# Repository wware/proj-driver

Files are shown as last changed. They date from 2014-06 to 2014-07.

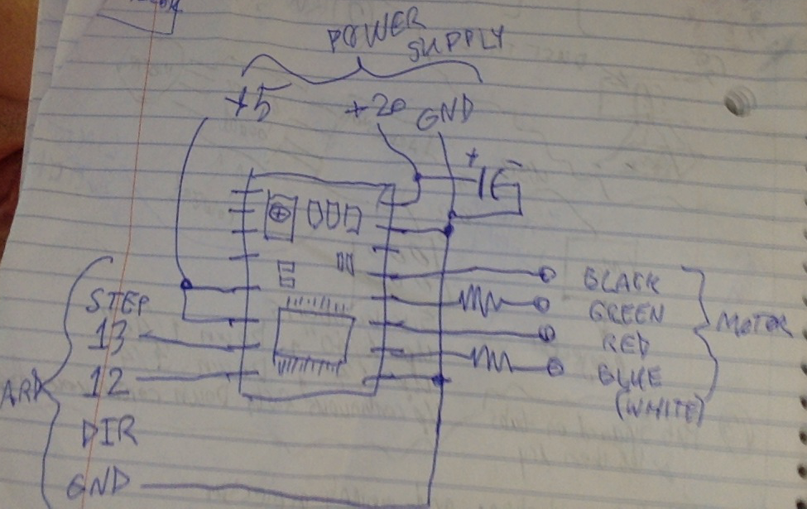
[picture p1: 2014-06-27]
arduino/StepperDriverSchematic.png

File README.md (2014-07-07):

Stereolithographic printer
==

[Blog post](http://willware.blogspot.com/2014/07/homebrew-stereolithographic-3d-printer.html)

A picture of the printer What it looks like

Initially I tried shooting the projector up through the bottom of a glass pie plate, and followed examples of coating the inside of the pie
plate with Sylgard 184. But I couldn't get the Sylgard to work correctly; the cured resin kept sticking to it instead of sticking to my
build platform. So I took a page from the [Peachy Printer](https://www.youtube.com/watch?v=80HsW4HmUes) and projected downwards into a
bucket where a layer of resin floats on a larger quantity of salt water, because resin is expensive and salt water is very cheap.

My long-term intent, once I get several bugs and issues sorted out, is to publish plans, schematics, and software on
[Github](https://github.com) and [Instructables](http://instructables.com) or similar websites, and put the entire thing either in the
public domain or under some reasonably permissive [Creative Commons](http://creativecommons.org/) license like
[BY-SA](http://creativecommons.org/licenses/by-sa/3.0/).

Projector
--

InFocus IN114A, unmodified, 3000 lumens, 1024x768 resolution, HDMI input, 190 watts, 110 vac, $349 with $6 shipping

* http://www.newegg.com/Product/Product.aspx?Item=0B1-00PJ-00003
* http://www.infocus.com/projectors/product?pn=IN114A

Browser stuff
--

You need a browser window on the Mac that can be updated when necessary, and you position that browser window image under the resin tub. This runs off a little CherryPy server on the Mac. The home page that the browser visits has Javascript which hits an endpoint asking for an numerical index and a number of seconds. This polling happens fairly frequently (once or twice a second).
The file with that metadata is at `static/image.info` and is expos1ed with a URL of `/info`. The image is stored at `static/image.png` and
is exposed with a URL of `/image`. You don't want to use CherryPy's static mechanism to read these files, because they get cached and then
you don't get updated when they change.

If the JS hasn't seen that index before (which simply increments) then it un-hides an image element for that number of seconds.

The background of the web page is black so as to not cure any resin unnecessarily.

I might need [templating](https://bitbucket.org/Lawouach/cherrypy-recipes/src/tip/web/templating/).

On the Mac, use Cmd-Shift-F to make a browser tab take up the full screen.

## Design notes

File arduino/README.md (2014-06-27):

Arduino code
==

The Arduino has the job of driving the stepper. It communicates over USB-serial with the
host machine. (The host machine also drives the projector.) I'm using a Macbook for the
host machine but there is no reason you couldn't use a Windows or Linux machine.

The serial protocol works like this. You type a letter (j, J, k, K, U, I) and in respponse
the motor moves the carriage up or down by some amount. The mnemonic is the vi commands:
Lower-case j and k respectively move the carriage down and up by 1/40 inch. Upper-case J
and K respectively move the carriage down and up by 1/4 inch. Upper-case U and I
respectively move the carriage down and up by 2.5 inches. Since the threaded rod is
20 threads per inch, the small step is a half-rotation of the threaded rod, or 90 steps
of the NEMA-23 stepper motor.

Any other characters typed will be echoed, but won't move the motor. These letters will
be echoed at the end of the carriage movement. While the carriage is in motion, any
characters typed should be ignored.

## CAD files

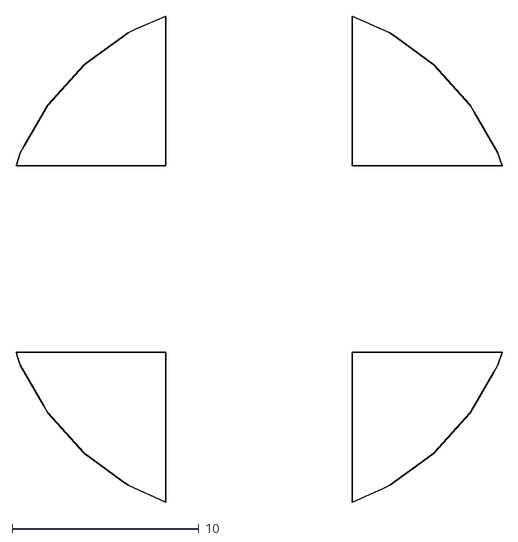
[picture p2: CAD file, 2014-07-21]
foo.dxf
26.0 x 26.0

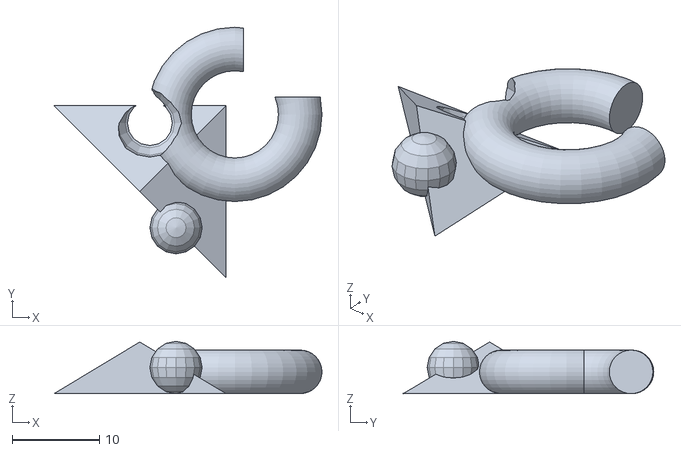
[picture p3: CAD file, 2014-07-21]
example.stl
30.7 x 28.7 x 6.00

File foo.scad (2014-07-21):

module example002()
{
    intersection() {
        difference() {
            union() {
                cube([30, 30, 30], center = true);
                translate([0, 0, -25])
                    cube([15, 15, 50], center = true);
            }
            union() {
                cube([50, 10, 10], center = true);
                cube([10, 50, 10], center = true);
                cube([10, 10, 50], center = true);
            }
        }
        translate([0, 0, 5])
            cylinder(h = 50, r1 = 20, r2 = 5, center = true);
    }
}

projection(cut = true) example002();

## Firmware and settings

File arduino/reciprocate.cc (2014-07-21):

int DIRECTION = 12, STEP = 13;

void setup() {
    pinMode(STEP, OUTPUT);
    pinMode(DIRECTION, OUTPUT);
    digitalWrite(STEP, LOW);
    digitalWrite(DIRECTION, LOW);
}

void briefWait() {
    delayMicroseconds(1000);
}

void run_motor(int dir, int steps) {
    digitalWrite(DIRECTION, dir);
    while (steps > 0) {
        briefWait();
        digitalWrite(STEP, HIGH);
        briefWait();
        digitalWrite(STEP, LOW);
        steps--;
    }
}

void loop() {
	run_motor(0, 1000);
	delayMicroseconds(1000000);
	run_motor(1, 1000);
	delayMicroseconds(1000000);
}

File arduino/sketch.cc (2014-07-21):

#include <stdlib.h>

char buf[10];
int bufptr;

int DIRECTION = 12, STEP = 13;

void setup() {
    Serial.begin(9600);
    pinMode(STEP, OUTPUT);
    pinMode(DIRECTION, OUTPUT);
    digitalWrite(STEP, LOW);
    digitalWrite(DIRECTION, LOW);
    bufptr = 0;
}

void briefWait() {
    delayMicroseconds(1000);
}

void run_motor(int dir, int steps) {
    digitalWrite(DIRECTION, dir);
    while (steps > 0) {
        briefWait();
        digitalWrite(STEP, HIGH);
        briefWait();
        digitalWrite(STEP, LOW);
        steps--;
    }
}

void loop() {
    int dir, steps;
    char c;
    while (Serial.available()) {
        buf[bufptr++] = c = (char)Serial.read();
        if (c == '\n') {
            steps = atoi(buf);
            if (steps < 0) {
                dir = 1;
                steps = -steps;
            } else {
                dir = 0;
            }
            run_motor(dir, steps);
            Serial.println("OK");
            bufptr = 0;
            return;
        }
    }
}

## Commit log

2014-06-27 Arduino stuff, but bad motor wiring???
2014-06-30 Image generation: try to print an octahedron
2014-07-21 Begin working with STL files.
    [example.stl]
2014-07-21 Working on Arduino stuff
2014-07-21 Use OpenSCAD to generate DXF from a slice of a STL.
    /Applications/OpenSCAD.app/Contents/MacOS/OpenSCAD foo.scad -o foo.dxf
    [foo.dxf, foo.scad]
2014-07-22 Mock out stepper for now, make arduino a module.
2014-07-22 Lots of changes now that stepper is finally ready
